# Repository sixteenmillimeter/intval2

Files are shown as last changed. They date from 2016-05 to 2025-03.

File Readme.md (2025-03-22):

# INTVAL 2.0
##### Intervalometer for Bolex 16mm Cameras

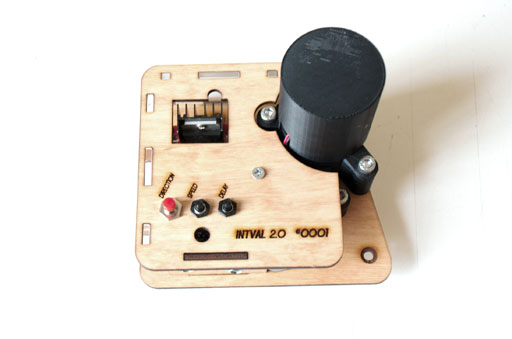
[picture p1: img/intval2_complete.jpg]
Photo of finished INTVAL


## [Project Home - git.sixteenmillimeter.com/16mm/intval2](https://git.sixteenmillimeter.com/16mm/intval2)

#### Github Mirror - [github.com/sixteenmillimeter/intval2](https://github.com/sixteenmillimeter/intval2)

----

 1. [Overview](#Overview)
 2. [Attachment](#Attachment)
 3. [Usage](#Usage)
 4. [Power](#Power)
 5. [Creating Your Own](#Creating)

----
### 1) Overview 

The INTVAL 2.0 is an open-source open-hardware intervalometer for Bolex 
16mm cameras. It enables you to expose single frames of film
at a regulated interval. Utilizing the 1:1 shaft in Bolex cameras (**Rex
4 and later models**) the INTVAL 2.0 can complete a full rotation of the shutter
in either 1 or 2 seconds. This allows for a range of long exposure options when
used in concert with the Rexofader.

----
### 2) Attachment

To attach the INTVAL 2.0 to a Bolex camera, disable the motor and line up the four standoffs
with the mounting holes on the body of the camera and insert the key into the 1:1 shaft. 
This can be done by laying the camera on its side--with the mounting holes facing up--and placing the INTVAL 2.0 on top of the body and making sure the key fits into the slotted 1:1 opening.
If you have never attached anything to the mounts before, you may have to 
remove small screws that are in the holes. This opens up the mounting holes for 
the screws that will hold the intervalometer in place. There are four standoffs
and screws, but only three need to be attached to maintain the hold required for operation.

----
### 3) Usage

The INTVAL 2.0 has two physical interfaces: the buttons on the case and the shutter
release cable. The shutter release cable plugs into the underside of the case, next
to the DC adapter, and triggers the camera. A single, short press will trigger a ``single
frame``. Holding down the shutter release for more than 1 second will start a ``continuous sequence``
of frames. Hitting the shutter release during a running sequence will stop the intervalometer.

The buttons on the case control three variables: direction, speed and delay. The direction of the
camera can be set to ``forwards`` (default) with a quick press, and set to ``backwards`` by holding the
button for more than 1 second. 

Similarly, the speed can be set to ``1 second rotation`` (default) with a
quick press and set to ``2 second rotation`` by holding the button for more than 1 second. Remember,
during the 1 or 2 seconds that the shutter is rotating, exposure only occurs for a fraction of that time. How large a fraction depends on the setting of the Rexofader.

Delay refers to the time the intervalometer pauses between frames and only matters when running a sequence. The delay is set to ``42 ms`` by default and will be set to however long you hold it down for; holding the button for``10 seconds`` will set the delay between each frame to ``10 seconds``. Pressing the button quickly will reset the timer to the default ``42 ms``.

----
### 4) Power

Power the INTVAL 2.0 with 12VDC to the 2.1mm DC power jack located on the bottom of the case.
The maximum draw of the motor is under 1 Amp, so that much current should be ample to run the
intervalometer. Portable batteries, such as those used as supplimental cellphone power supplies, 
can be used to as mobile power sources, but they must be able to provide 12V and not the typical 5V that many of these batteries provide. 

Two examples: 

[Anker 2nd Gen Astro Pro2 20000mAh 4-Port Aluminum Portable External Battery Charger with 9V/12V Multi-Voltage Port](http://www.amazon.com/gp/product/B005NGLTZQ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)

[ Rechargeable 3800mAh Lithium Ion Battery Pack with DC Connector, 12 volt](http://www.amazon.com/gp/product/B007RQW5WG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)

12V wall warts that can provide 1 Amp or over are also viable options for shooting in a controlled environment.

----
### 5) Creating Your Own

All parts of the INTVAL 2.0 are reproducible via 3D printing, laser cutting or are purchasable (example links are to Amazon or [Adafruit](http://adafruit.com)) for a total build cost of ~$50. The files in this repository consist of .SCAD, .STL, .DXF and .INO files. The .SCAD files contain all the elements needed to generate the physical body of the intervalometer with .DXF files for
laser cutting and .STL files for 3D printing. The .INO file contains the source code for the Arduino sketch that powers the INTVAL 2.0.

#### A. 3D Printing

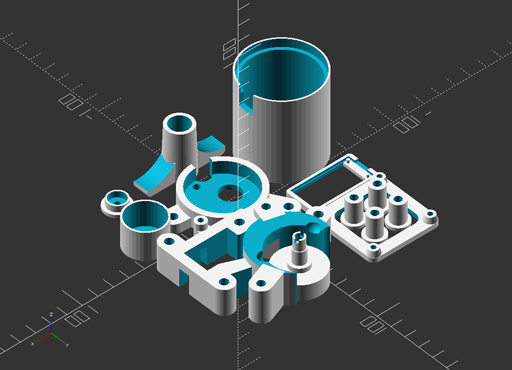
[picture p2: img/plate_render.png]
Plate of all 3D printed components


The most time-consuming part of this build *should* be 3D printing the parts for the INTVAL 2.0. Depending on the size of your printing bed it is most likely possible to print all parts in one convenient plate. As will be addressed later, the laser-cuttable elements can also be 3D printed if you lack access to a laser cutter. 

In the ``/dist`` directory of the repo, you will find all of the .STL files needed to build the intervalometer. If needed, the .SCAD file can be used to generate additional .STL models, or it can be modified to produce unique parts to your own specifications.

The most delicate and integral piece to be fabricated on a 3D printer is the ``motor_key``, which interfaces the intervalometer to the 1:1 shaft of the Bolex. This part should be printed as close to solid as your printer allows or you should look at a third-party printing service to have it made from stronger materials than the typical PLA or ABS used by most home printers. That said, I have used an ABS-printed motor key extensively with no issues thus far.

#### B. Laser Cutting

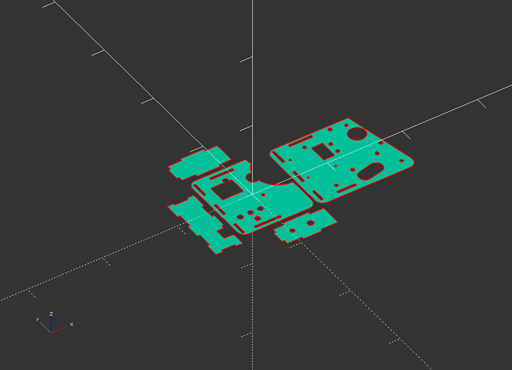
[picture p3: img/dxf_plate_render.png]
Plate of all laser cut components


The INTVAL 2.0 has a flat panel on which all parts and electronics are mounted. For this reason, and to reduce production time, a laser cutting component has been added. See the much earlier--and now deprecated--attempt to have an entirely printable model in the original [INTVAL](https://github.com/sixteenmillimeter/INTVAL) (or [INTVAL Next](http://www.thingiverse.com/thing:151944) as I had taken to calling it on [Thingiverse](http://thingiverse.com)). Printing the flat base of this version took upwards of 3 hours on my modest printer, and with the accessibility of laser cutters at hacker/maker spaces becoming more common I decided this was feasible to include in my design.

Important to note: **A laser cutter is not required to make this intervalometer.** If you have access to a 3D printer, it's very possible to use the .SCAD files to generate .STLs of the parts designated for cutting. Make sure that they are all set to 3.175mm thickness as the design requires 1/8" materials for assembly. A clever person could even improve the design to remove the need for bolts to attach the ``motor_mount_bottom`` and ``electronics_mount`` pieces when making a 3D printed version.

Another note: When cutting the base of the intervalometer, named the ``panel_laser`` there is a circular cut for a skateboard wheel bearing to be inserted. These are made with slightly different tolerances, so do some tests before you cut your final panel. When properly scaled, the bearing should fit tightly so that it can be glued to the panel. The positioning of the bearing is vital to the functionality, so it's best to test the bearing fit using the ``bearing_calibrate`` module and then edit the size of the bearing by changing the  ``fuzz`` variable of the ``bearing_laser`` module. Export a new .DXF of the ``intval_panel_laser`` module by using the ``projection()`` function and cut that.

##### Materials

Early prototypes for the INTVAL 2.0 were made with 1/8" acrylic. I was very hopeful that I would be able to make a visually clear product where all of the electronics would be visible. Cool, right? This, unfortunately, was not to be. The forces applied to the prototypes during casual use would cause the acrylic to crack or shatter quite easily. I'm not saying it's not possible, but just that it is a less-than-ideal material for this project.

Here's what I would suggest, in order (all should be cut from 1/8" sheets):

 1. Craft plywood - Cheap, flexible and effective. I cut this, add custom designs, stain and coat in polyurethane. Yet to have any issues with it.
 2. Delrin (acetal homopolymer) - Too rich for my blood, but should perform better than acrylic. Will probably look pretty cool.
 3. Acrylic - Good for prototyping, but may crack under pressure. Make parts to spare if you go down this path.

#### C. Hardware

I would like to further reduce the amount of non-fabricated parts required for this build in future revisions, but here we are. I've run a few spreadsheet models and have the cost-per-unit down to ~$50, but this fails to account for shipping, misprints and a whole host of associated costs, including build time. Needless to say, I don't see a profitable enterprise being build on the production of 16mm intervalometers, which is why I am creating this in the open for others to build and improve upon. 

Links below are to Amazon for accessibility and [Adafruit](http://adafruit.com) where possible, but feel free source compatible or equivalent materials from companies that align to your personal ethics. Sourcing from AliExpress can bring the cost-per-unit down dramatically, if you are building these as part of a workshop or class.

The meat of this project are the L298N Dual H-Bridge and the Arduino Trinket 5V. The 3D models are designed for the 60RPM motor listed below, but the design can easily be adapted to other motors. I'm trying out other motors in a few different forks of this project.

All of the purchasable parts for this build:

1. (1x) Arduino Trinket Pro 5V - [[Adafruit](https://www.adafruit.com/products/2000)] [[Amazon](https://amzn.to/2WdVimL)]
3. (1x) 120RPM 12VDC Motor - [[Amazon](https://amzn.to/2YDGFe2)]
4. (1x) L298N Breakout Board - [[BC Robotics](https://www.bc-robotics.com/shop/l298n-motor-driver-board/)] [[Amazon](https://amzn.to/35CRFKa)]
5. (1x) Microswitch w/ Roller - [[Adafruit](https://www.adafruit.com/product/819)] [[Amazon](https://amzn.to/2YDGFe2)]
6. (1x) 3.5mm Socket Audio Connector - [[Amazon](https://amzn.to/2SGFVAY)]
7. (1x) 3.5mm Stereo Audio Cable - [[Amazon](https://amzn.to/3beNPrQ)]
8. (4x) Momentary Push Button 7mm Diameter - [[Amazon](https://amzn.to/2LavqBK)]
 8. (1x) Micro Switch w/ Roller Lever 28mm x 30.2mm x 10.2mm - [[Adafruit](https://www.adafruit.com/products/819)] [[Amazon](https://amzn.to/2SMBFzX)]
 9. (1x) Skateboard bearing 608-2RS - [[Amazon](https://amzn.to/3b7X2lC)]
 10. (4x) M3.5 - 0.6 x 20mm Screws
 11. (3x) M2 - 0.6 x 15mm Bolts
 12. (6x) M5 - 0.8 x 25mm Bolts
 13. (4x) M5 - 0.8 Nuts

Additionally you'll need wire and solder of your choosing.

#### D. Assembly

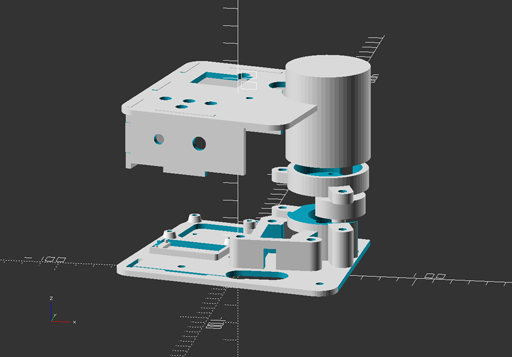
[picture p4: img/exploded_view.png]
Photo of exploded view


Assembling the INTVAL 2.0 can be done in an hour or so, much quicker if practiced. As mentioned, the largest amount of time should be in fabricating the parts or acquiring electronics/parts. There are 2 things I don't like about this design that I'll be addressing in subsequent builds: complexity of the electronics and crowding inside the case.

##### **Mounting the electronics**

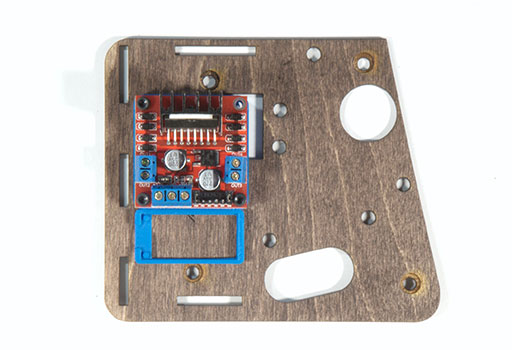
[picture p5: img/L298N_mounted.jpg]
Photo of L298N mounted to panel


The L298N is attached to the panel via the three M2 bolts. The space cut in the panel where the fourth would go is to prevent the Bolex's handle from rubbing against the panel. At this point I usually flash the Arduino Trinket Pro with the latest firmware, as in the ["Programming"](#Programming) section, prior to soldering and mounting. It can be done after, though, and can be reprogrammed after it is built.

##### **Attaching the bearing**

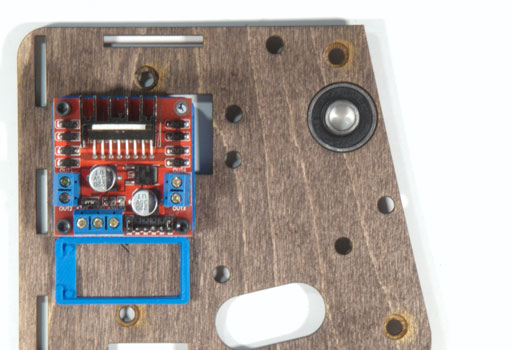
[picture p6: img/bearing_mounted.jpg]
Photo of panel with bearing attached


##### **Mounting the motor's base and microswitch**

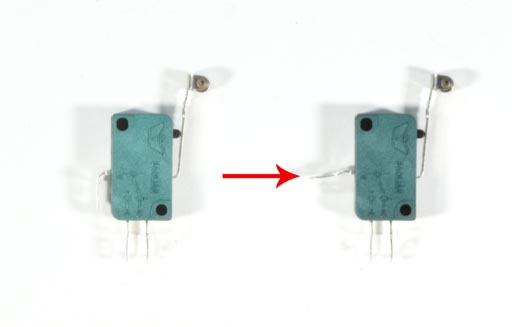
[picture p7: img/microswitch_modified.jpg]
Photo of Microswitch and modification made to it


Modify the microswitch as shown in the photos. Be careful not to break the tab by over-exerting it at the bend. At this point, I usually solder leads onto the two tabs as shown below to save a cramped soldering job later. Insert the microswitch into the ``motor_mount_bottom`` and line the piece up with the 6 holes cut in the panel according to the pictures and rendering. It then gets attached to the panel with 4 of the M5 bolts and attached on the bottom with the corresponding M5 nuts.

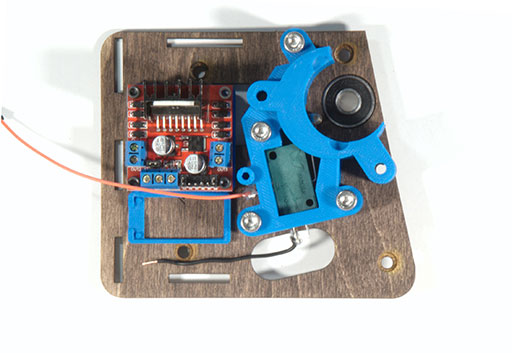
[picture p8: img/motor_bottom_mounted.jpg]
Photo of panel with motor mount bottom attached


##### **Mounting the motor**

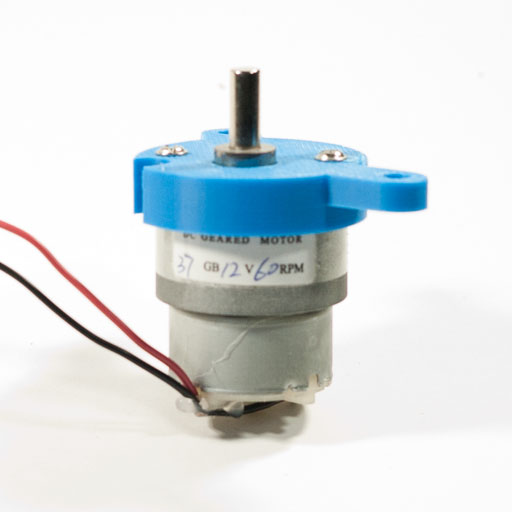
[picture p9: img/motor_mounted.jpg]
Photo of motor ready to mount on panel


The motor should fit snugly into the ``motor_mount`` piece and can be attached with 2 screws that usually accompany the motor (when bought from Amazon). At this point, I usually solder 2 leads onto the top of the motor and cap it so that the fragile tabs wont break off. I use red and black wires so that I can easily switch their position in the L298N if the intervalometer is functioning backwards.

##### **Attach buttons**

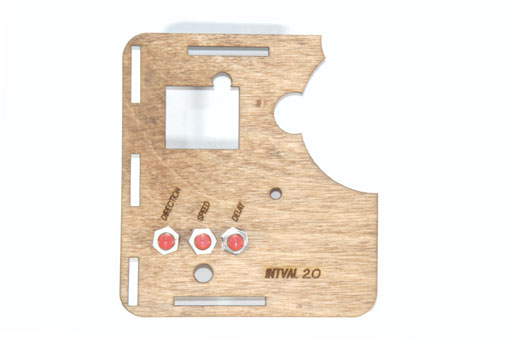
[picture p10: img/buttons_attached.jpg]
Photo of buttons attached to panel cover


Three of the buttons are attached to the corresponding holes in the panel. The size of these holes might have to be modified depending on the type of momentary buttons you settle on. When cutting the panel cover, I will also add an etched-in label for each specifying (left to right) that they control ``direction``, ``speed``, and ``delay``.

##### **Attaching the DC and 3.5mm sockets**

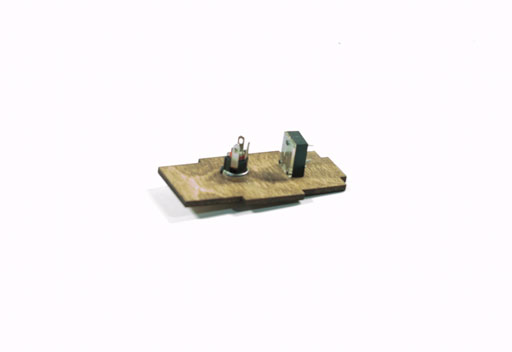
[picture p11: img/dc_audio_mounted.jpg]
Photo of DC and 3.5mm sockets on


Attach the 2.1mm DC socket and the 3.5mm audio socket to the bottom panel of the board, using the bolts to secure them. 

#### E. Soldering

Use of the $10 [Arduino Trinket Pro 5V](https://www.adafruit.com/products/2000) is explicitly due to the number of buttons required for the user interface. If you wanted to drop one of the buttons, say the speed control, you could re-write the sketch to use a $7 [Arduino Trinket 5V](https://www.adafruit.com/products/1501) (or get them in bulk for more savings). I mention this because it was the target microcontroller breakout for the project but had to be upgraded to the pro model to support all of the features in the design.

Digital pin utilization is as follows:

- **PIN 3** - Shutter release
- **PIN 4** - Delay button
- **PIN 5** - Speed button
- **PIN 6** - Direction button
- **PIN 9** - Motor forward (L298N)
- **PIN 10** - Motor backward (L298N)
- **PIN 13** - LED indicator (built in to Trinket Pro)
- **PIN 19** - Microswitch (aka A5)

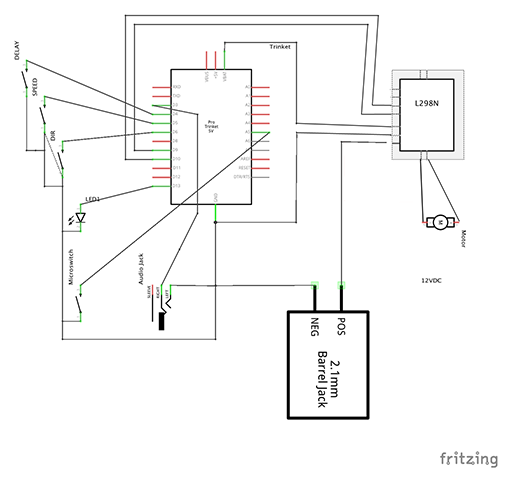
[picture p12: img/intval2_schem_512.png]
Fritzing schematic


The Fritzing project requires the following libraries:

 1. [Adafruit Fritzing library](https://github.com/adafruit/Fritzing-Library)
 2. [L298N Dual H-Bridge library](https://github.com/yohendry/arduino_L298N)

#### E. Building the shutter release (plunger)

To trigger the intervalometer and to start/stop sequences, the INTVAL 2.0 uses a simple switch that I found is handily made from cheap audio parts. In a pinch, this switch can be hard-wired into the design, but for the safety of the electronics inside I decided on using a 3.5mm socket and 3.5mm cable with a simple momentary button closing the circuit. For this, I buy a 6' cable and cut it in two.

Pull the cable through the small bottom cap of the plunger body (important) and solder both of the leads to the two tabs of the button. The bottom cap might have to be modified to better accommodate the size of the 3.5mm audio cable you end up using. Insert the button into the plunger body and fasten with the nut provided with the button. Then attach the bottom cap to the body. At this point, I usually use hot glue to prevent too much force being applied to the solder points.

#### G. Programming

This step should be done carefully, and with some practice. For a good primer on the basics of programming the microcontroller, check out Adafruit's [tutorial on it](https://learn.adafruit.com/introducing-pro-trinket/starting-the-bootloader). Arduino Trinket Pros enter into a short firmware-writable state when first plugged into a USB source. This is marked by the pulsing of the red indicator LED on the board.

If using the Arduino IDE, make sure you have the latest version and have read through [this primer](https://learn.adafruit.com/introducing-pro-trinket/setting-up-arduino-ide) before you try to upload the sketch to the Trinket Pro. While the red LED is flashing, upload the sketch provided in this repository and that's it. Any modifications to the code can be made and flashed onto the board as many times as you'd like. Please feel free to submit pull requests if you make any improvements!

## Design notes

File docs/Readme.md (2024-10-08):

# intval2 Quickstart

## Attaching

1. Disengage the Bolex motor by switching the lever at position **M** to **O**.
2. Set the camera trigger to **M** (opposite **P**).
3. Place the intval2 on the camera, lining up the 4 standoff posts with the 4 exposed metal mounting points.
4. Line up the intval2 key to the Bolex 1:1 shaft so that it fits snugly.
5. Place the 3.5mm screws into 3 of the standoffs, one above the 1:1 shaft, one below and the other in the back top area of the intval2. The standoff underneath the buttons is not accessible.
6. Tighten the 3.5mm screws to secure the intval2 to the Bolex.

## Powering

Power the device using a 12V DC power source with a 2.1mm center-positive barrel connector.
Ensure that the power supply can output at least 1 Amp to ensure there is enough force to drive the motor.
You can use a portable battery designed for recharging phones as long as it is capable of outputting 12V.

Plugging and unplugging the shutter release cable will trigger a frame so ensure that it is plugged in before powering on and removed before powering off if you do not want to unexpectedly advance or rewind the camera.

## Using

Using the intval2 is simple and relies on the settings made available by the 3 buttons on the side and the shutter release cable.

### Shutter Release

The shutter release cable uses a 3.5mm audio cable and a simple switch to trigger a frame.
Pressing the shutter release cable button for longer than 1 second and releasing starts timelapse mode where the camera will shoot frames continuously.
The other buttons change settings that will take effect when you trigger each frame.

Keep in mind that plugging and unplugging the cable while the intval2 is powered on and attached to a Bolex will trigger a frame.

### Direction

The direction button, labeled "DIR" and usually red, will change the direction of the camera from forward to reverse by pressing it for longer than 1 second.
Press it for less than 1 second to reset it to forward.

### Exposure

In normal mode the camera completes a frame in ~500ms, which after accounting for the shutter angle and the prism light loss, is roughly equivalent to 1/5 second exposure.

Change the exposure of the camera by pressing the button "EXP", usually green, for longer than 1 second.
However long you press the button is how long an exposure the camera will make.
Once set an exposure will be taken by opening the shutter, waiting for the appropriate amount of time, and then closing the shutter.
Press the button for less than 1 second to restore normal exposure.

### Delay

The "delay" feature determines how long between frames the intval2 will wait when running in timelapse mode.

Change the delay between frames by pressing the "DEL" button, usually blue, for longer than 1 second.
Similar to the others, press it for less than 1 second to reset the delay to 0.

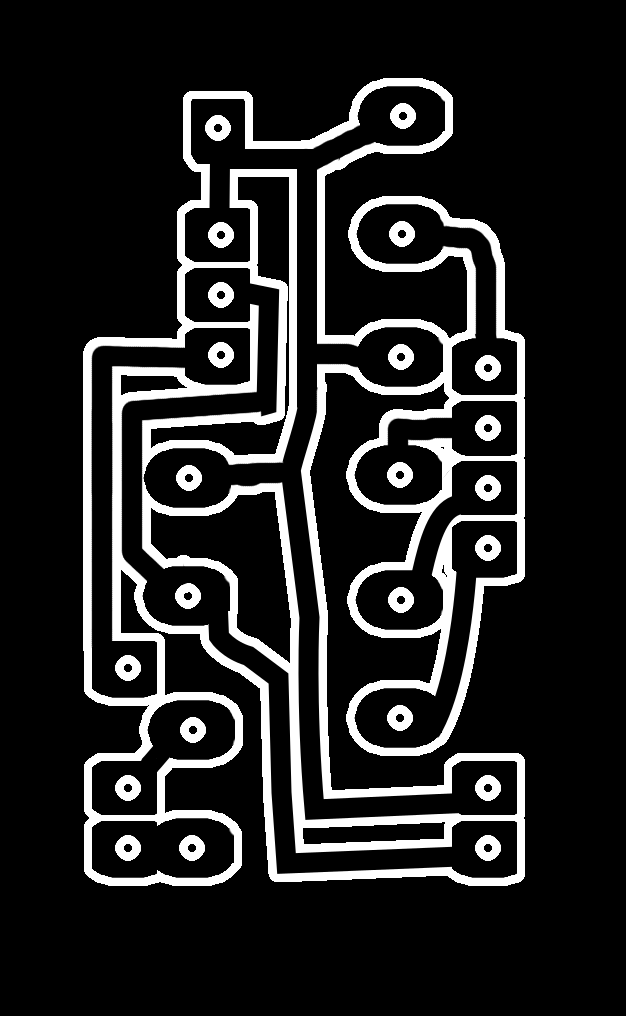
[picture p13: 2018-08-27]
dist/intval2_shield_etching/intval2_shield_servo_v2.png

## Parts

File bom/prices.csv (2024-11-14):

part | part_id | price | url
DC Power Jack | N/A | 110 | https://amzn.to/4evqnHx
12V 120RPM Geared Motor 37mm Gearbox | N/A | 1499 | https://amzn.to/3YQo1ge

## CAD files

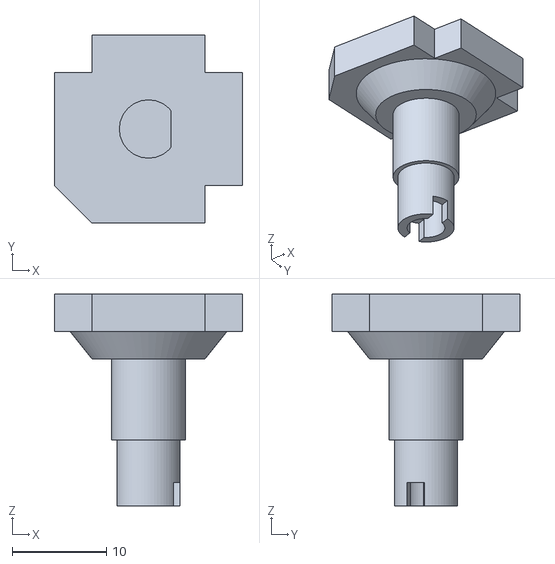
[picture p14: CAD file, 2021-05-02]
dist/intval2_motor_key_reinforced.stl
20.0 x 20.0 x 22.5

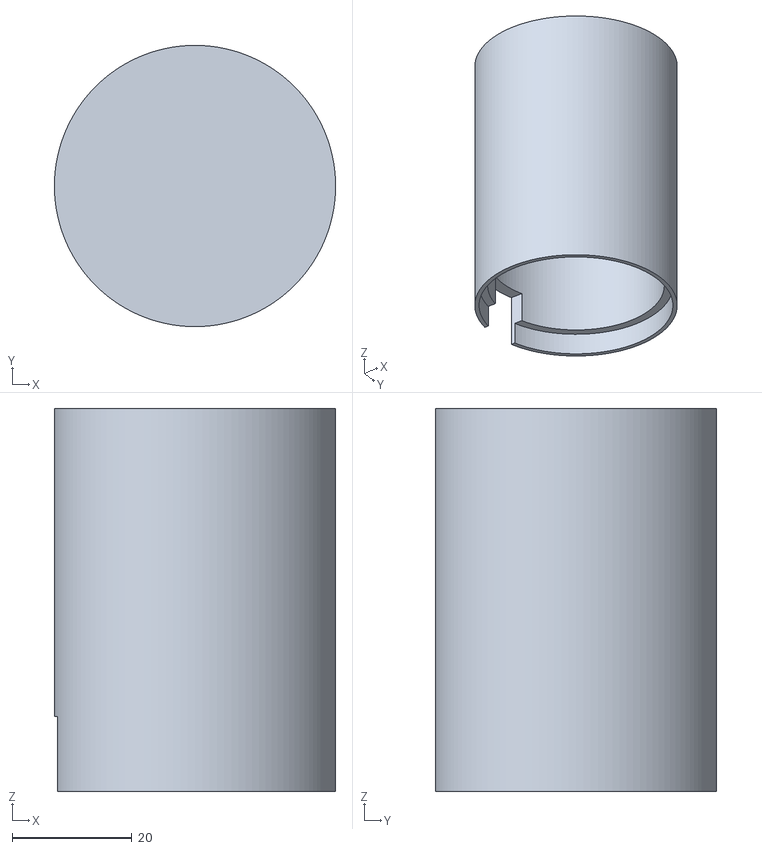
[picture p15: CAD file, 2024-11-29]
stl/intval2_motor_cap_alt.stl
47.0 x 47.0 x 64.0

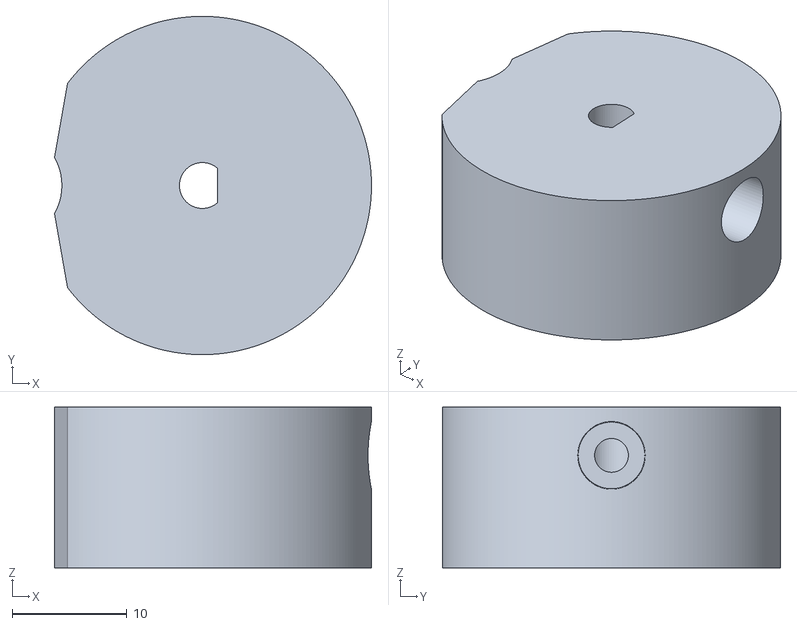
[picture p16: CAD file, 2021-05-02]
dist/intval2_motor_key_120_reinforced_roller.stl
27.6 x 29.5 x 14.0

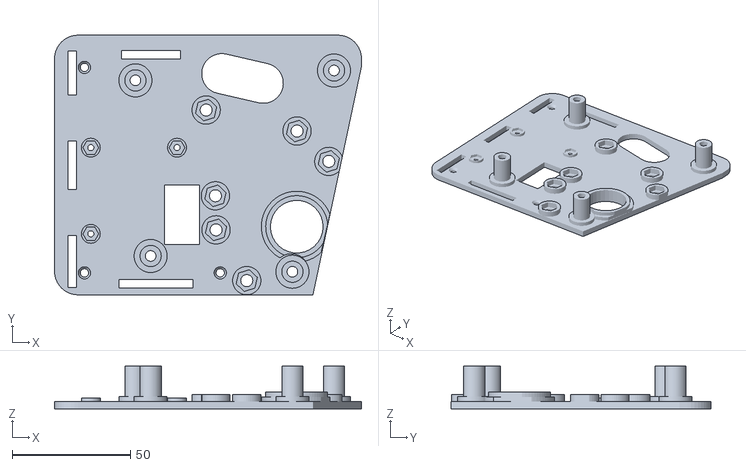
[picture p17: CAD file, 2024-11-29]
stl/intval2_printed_panel.stl
130.0 x 110.0 x 18.2

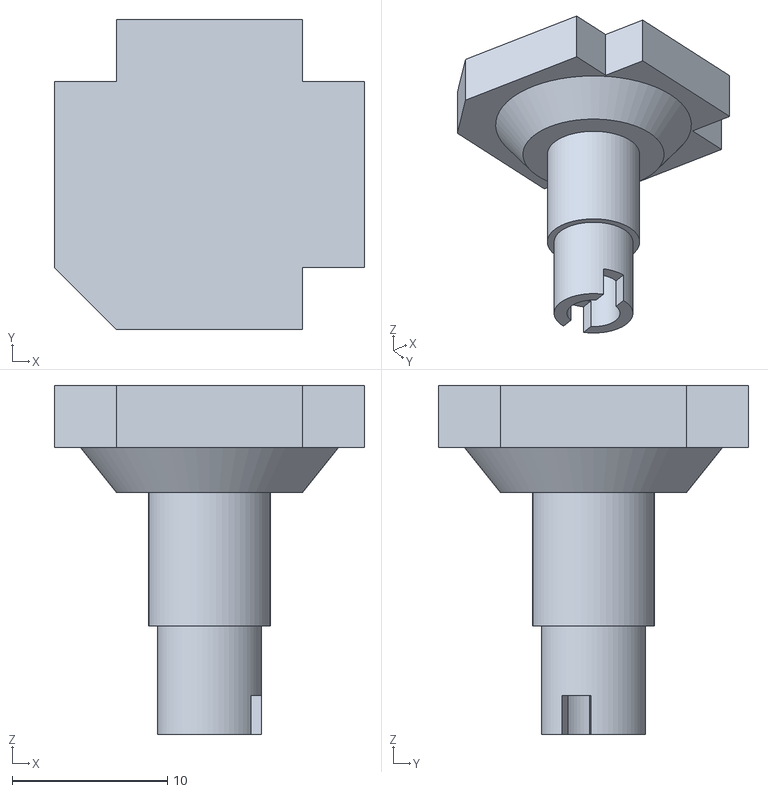
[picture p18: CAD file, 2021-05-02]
dist/intval2_motor_key_120_reinforced.stl
20.0 x 20.0 x 22.5

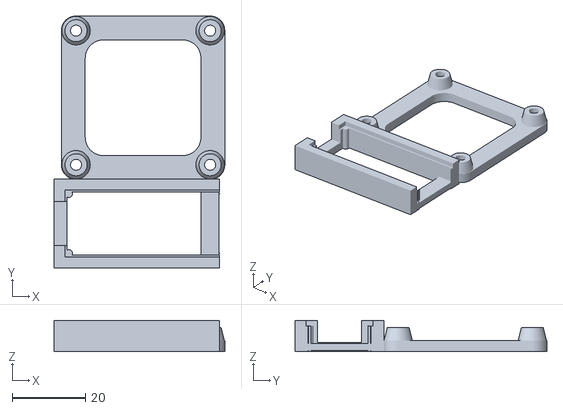
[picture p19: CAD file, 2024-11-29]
stl/intval2_arduino_nano_electronics_mount.stl
46.5 x 68.6 x 8.50

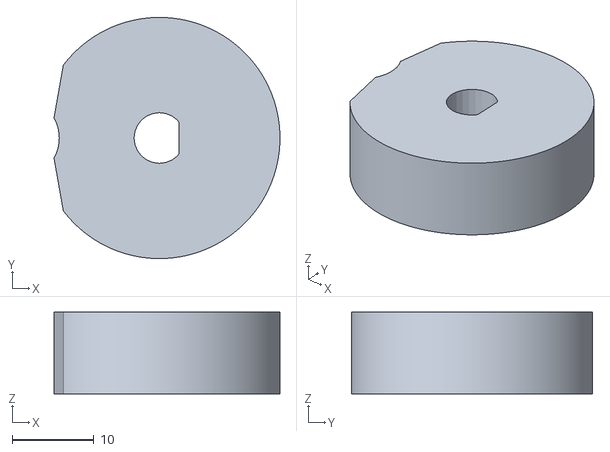
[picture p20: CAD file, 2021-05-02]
dist/intval2_motor_key_reinforced_roller.stl
27.6 x 29.5 x 10.0

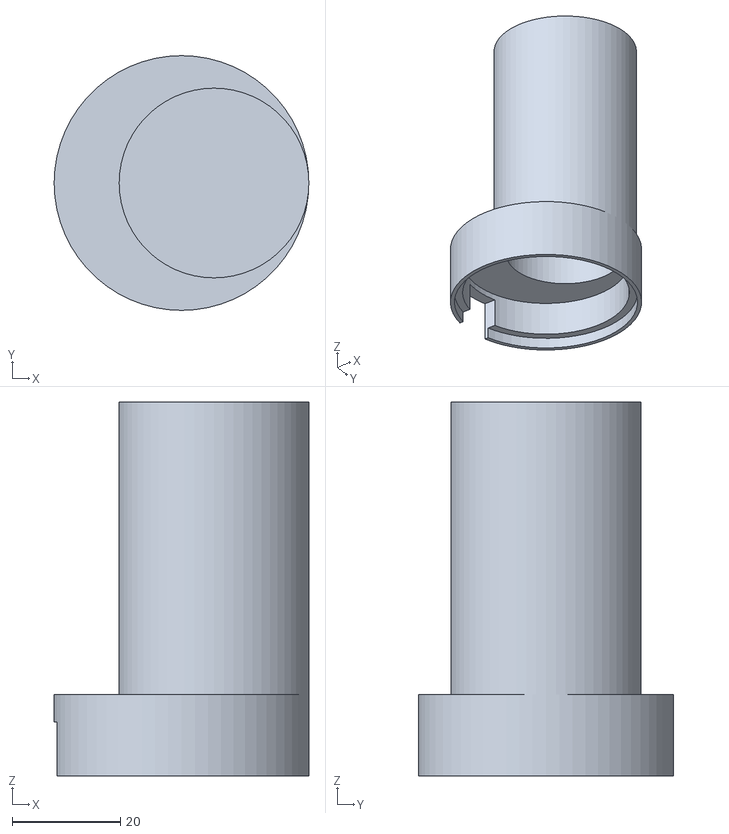
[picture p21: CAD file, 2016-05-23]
dist/intval2_motor_cap_120.stl
47.0 x 47.0 x 69.0

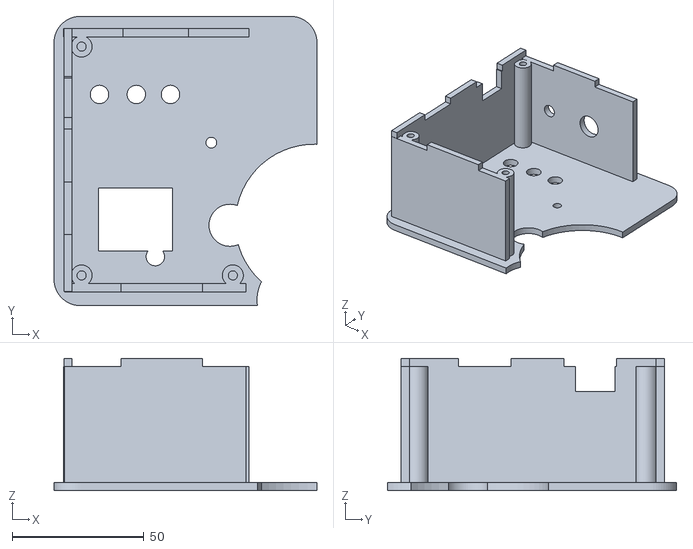
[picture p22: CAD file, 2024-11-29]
stl/intval2_printed_panel_cover_buttons.stl
100.0 x 110.0 x 50.4

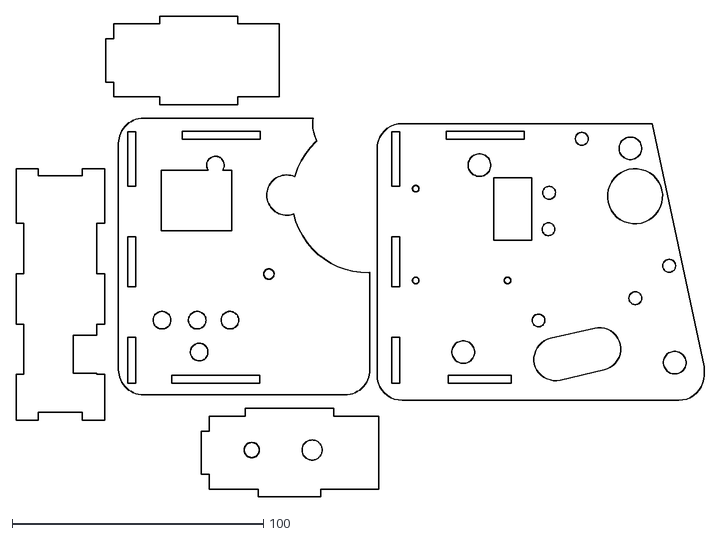
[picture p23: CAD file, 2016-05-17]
dist/intval2_dxf_plate.dxf
273.6 x 191.2

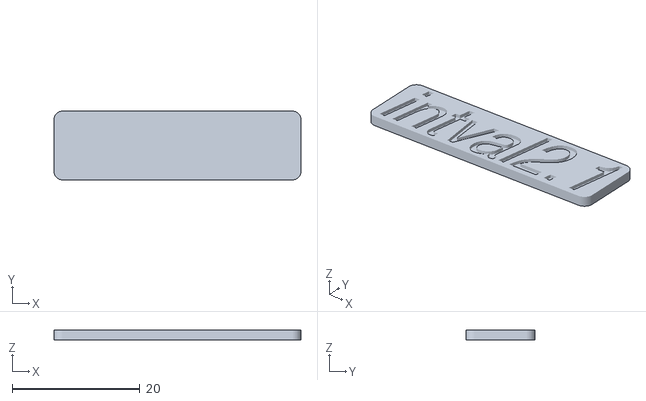
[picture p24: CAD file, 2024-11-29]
stl/intval2_logo.stl
38.7 x 10.8 x 1.50

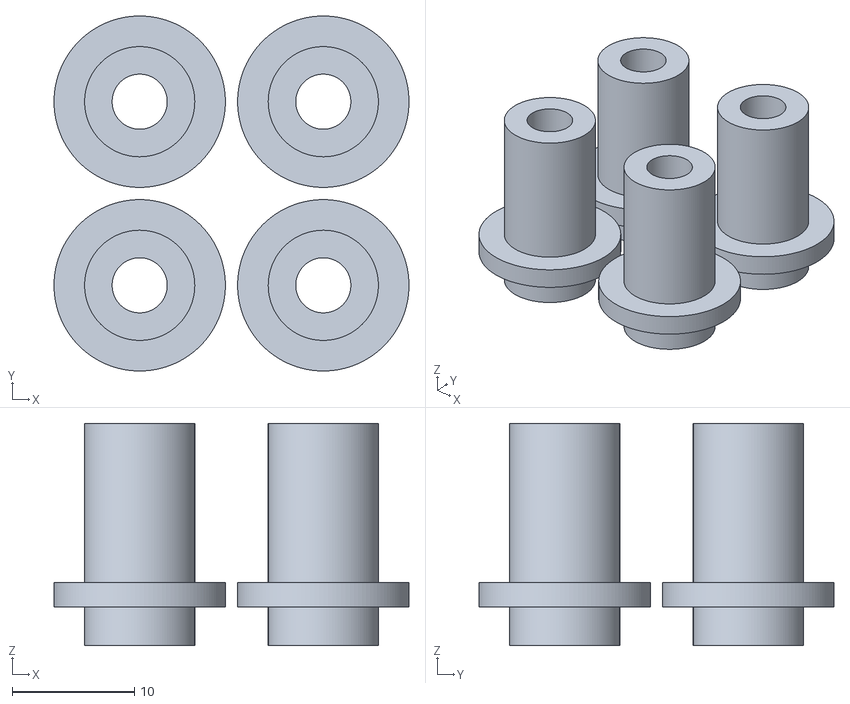
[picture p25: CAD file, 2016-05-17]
dist/intval2_standoffs.stl
29.0 x 29.0 x 18.2

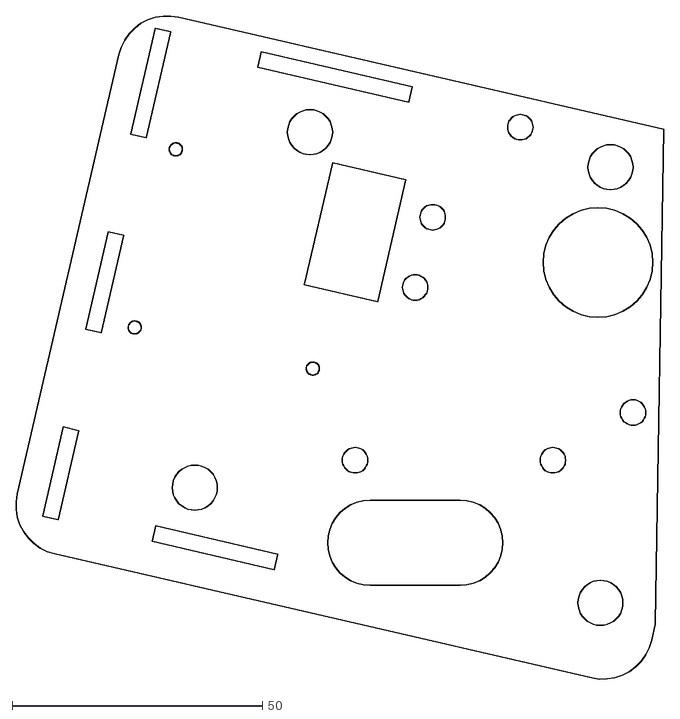
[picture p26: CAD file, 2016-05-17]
dist/intval2_panel_laser.dxf
129.4 x 132.4

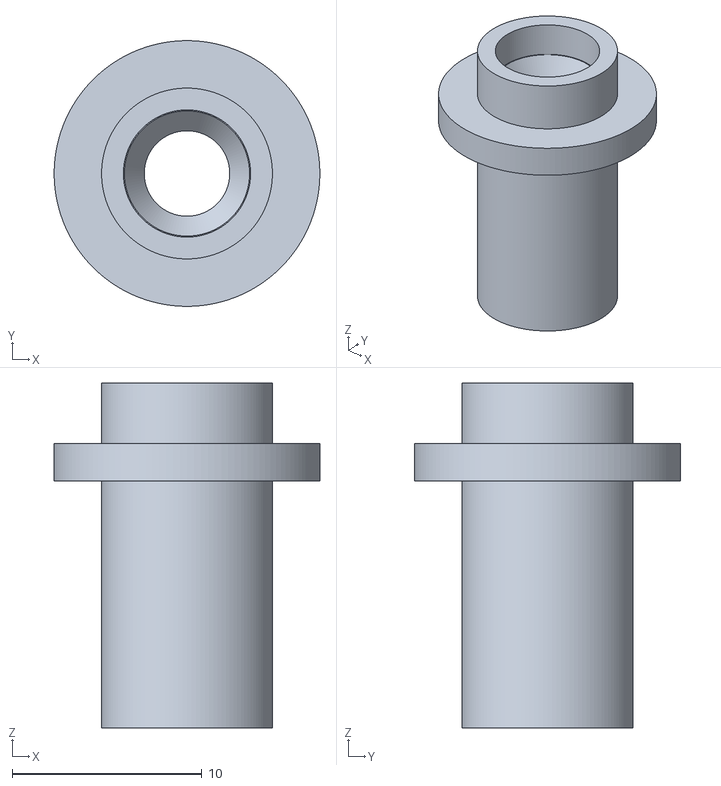
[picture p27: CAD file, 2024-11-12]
stl/intval2_standoff.stl
14.0 x 14.0 x 18.2

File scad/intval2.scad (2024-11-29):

include <./ready.scad>

mm_x = [61.5, 21.5, 6, 45.5, 18, 39];
mm_y = [-18, 21, -27.5, -27.5, 7, 39];
mm_r = [110, -15, 0, 0, 0, -70];
mm_l = [13, 9, 0, 0, 0, 8];
//xArray = [-3, 57,  55,  10, -26]; //WITH MIDDLE PIN
//yArray = [38, 31, -56, -22, -33]; //WITH MIDDLE PIN
xArray = [-3, 57,  55,  -26]; //NO MIDDLE PIN
yArray = [38, 31, -56,  -33]; //NO MIDDLE PIN

outerD = 9;
innerD = 4.5;
height = 17;

//panel_x = 129 + 4;
//panel_y = 131;
panel_2_x = 110;
panel_2_y = 110;

one_to_one_x = 54.5;
one_to_one_y = 12;

bolt_inner = 2.55;

screw_distance = 31;

module m5_nut_void (pos = [0, 0, 0]) {
    translate(pos) cylinder(r = 9.4 / 2, h = 4, $fn = 6, center = true);
}

module m5_nut_seat (pos = [0, 0, 0]) {
    $fn = 40;
    H = 4;
    translate(pos) difference () {
        cylinder(r = 12 / 2, h = H, center = true);
        cylinder(r = bolt_inner, h = H + 1, center = true);
        rotate([0, 0, 30]) m5_nut_void([0, 0, -1]);
    }
}

module m3_nut_void (pos = [0, 0, 0]) {
    translate(pos) cylinder(r = 6.7 / 2, h=3, center=true, $fn=6);
}

module m3_nut_seat (pos = [0, 0, 0]) {
    $fn = 40;
    H = 3;
    translate(pos) difference () {
        cylinder(r = 8 / 2, h = H, center = true);
        cylinder(r = 3.25 / 2, h = H + 1, center = true);
        m3_nut_void([0, 0, -1]);
    }
}

module l298N_nut_seats (r = 3/2 - .2, MOD_MOUNT = 0) {
    DISTANCE = 36.5 + MOD_MOUNT;

    m3_nut_seat([0, 0, 0]);
    m3_nut_seat([DISTANCE, 0, 0]);
    //m3_nut_seat([DISTANCE, DISTANCE, 0]);
    m3_nut_seat([0, DISTANCE, 0]);
}

module arduino_nano_mount (pos = [0, 0, 0]) {
    X = 18.2;
    Y = 43.9;
    Z = 10.5;
    BOARD_Z = 1.5;
    translate(pos) {
        difference () {
            //outer
            cube([X + 6, Y + 6, Z], center = true);
            //inner void minus corners
            difference () {
                cube([X - 1, Y - 1, Z + 1], center = true);
                translate([(X / 2) - 1, (Y / 2) - 1, -BOARD_Z]) cylinder(r = R(2), h = Z + 1, center = true, $fn = 20);
                translate([(-X / 2) + 1, (Y / 2) - 1, -BOARD_Z]) cylinder(r = R(2), h = Z + 1, center = true, $fn = 20);
                translate([(X / 2) - 1, (-Y / 2) + 1, -BOARD_Z]) cylinder(r = R(2), h = Z + 1, center = true, $fn = 20);
                translate([(-X / 2) + 1, (-Y / 2) + 1, -BOARD_Z]) cylinder(r = R(2), h = Z + 1, center = true, $fn = 20);
            }
            //board void
            translate([0, 0, (Z / 2) - (BOARD_Z / 2)]) cube([X, Y, BOARD_Z], center = true);
            //usb void
            translate([0, Y / 2, (Z / 2) - (6 / 2) + 0.01]) cube([12, 10, 6], center = true);
            translate([0, -30, 0]) cube([30, 20, 20], center = true);
        }
        translate([0, -(Y/2) + 4.5, -2]) cube([X + 5, 5, 2], center = true);
    }
}

module usb_mini_void (pos = [0, 0, 0]) {
    translate(pos) {
        translate([0, 25, 2]) {
            cube([8, 10, 5], center = true);
            translate([0, 5, 0]) cube([12, 10, 8], center = true);
        }
    }
}

module intval_panel_printed () {
	difference () {
        union () {
            intval_panel_laser(0.4);
		    for (i = [0 : len(mm_x) - 1]) {
                m5_nut_seat([mm_x[i], mm_y[i], 6]);
            }
            translate([-38, -1, 7]) rotate([0, 0, -13]) l298N_nut_seats();
            translate([0, 0, -0.6]) intval_laser_standoffs();
            translate([one_to_one_x, one_to_one_y, 5]) rotate([180, 0, 0]) bearing_reinforcement();
        }
        //onetoone(9, 14, 8.5);
		bearing(54.5, 12, 6, width= 18, hole=false);
		//frame_counter_access(); //use the space
		remove_front();
        printed_panel_bolts();
	}
}

module l298N_bolt_voids (r = 3/2 - .2, MOD_MOUNT = 0) {
    $fn = 60;
    DISTANCE = 36.5 + MOD_MOUNT;
    H = 50;
    translate([0, 0, 0]) cylinder(r = r, h = H * 5, center = true);
    translate([DISTANCE, 0, 0]) cylinder(r = r, h = H * 5, center = true);
    translate([DISTANCE, DISTANCE, 0]) cylinder(r = r, h = H * 5, center = true);
    translate([0, DISTANCE, 0]) cylinder(r = r, h = H * 5, center = true);
}

module l298N_hole_test () {
    $fn = 40;
    difference () {
        cube([140, 40, 3], center = true);
        cylinder(r = R(3), h = 50, center = true);
        for (i = [0 : 3]) {
            translate([7 + (i * 7), 0, 0]) cylinder(r = R(3) - (0.1 * i), h = 50, center = true);
        }
    }
}

module intval_panel_laser (pad = 0) {
    $fn = 40;
	difference () {
		union () {
			difference () {
				translate ([0, 0, 8.5]) {
					union () {
						translate([12, -5, 0]) {
                            rotate([0, 0, -13]) {
                                rounded_cube([panel_2_x + 20, panel_2_y, 25.4 / 8], d = 20, center = true);
                            }
                        }
					}
				}
				for (i = [0 : len(xArray) - 1]) {
					bolex_pin_inner_laser(xArray[i], yArray[i]);
				}
			}
		}
		bearing_laser(54.5, 12, 6, width= 18, hole=false);
        translate([-38, -1, 0]) rotate([0, 0, -13]) l298N_bolt_voids();
		m_p_access();
		remove_front();
		translate([6, 18, 0]) rotate([0, 0, -13]) cube([15, 25, 40], center=true); //motor wind key hole

		for (i = [0 : len(mm_x) - 1]) {
			translate([mm_x[i], mm_y[i], 0]) cylinder(r = bolt_inner, h = 100, center = true);
		}
        translate([0, 0, 0.3]) scale([1, 1, 1]) intval_laser_panel_cover(PAD = pad, BOLTS = false);
	}
}

module intval_panel_laser_debug () {
    $fn = 40;
	difference () {
		union () {
			difference () {
				translate ([0, 0, 8.5]) {
					union () {
						translate([-20.5, 4, 0]) {
                            rotate([0, 0, -13]) {
                                rounded_cube([panel_2_x + 85, panel_2_y, 25.4 / 8], d = 20, center = true);
                            }
                        }
						//reinforces
						//translate([54, -12, -3]) rotate([0, 0, 89]) rounded_cube([110, 20, 4], 20, center = true);
						//translate([-17, 2, -3]) rotate([0, 0, 72]) rounded_cube([94, 13, 4], 13, center = true);
					}
				}
				for (i = [0 : len(xArray) - 1]) {
					bolex_pin_inner_laser(xArray[i], yArray[i]);
				}
			}
			//onetoone(26, 10, 4.5);
			//extends for onetoone
			

		}
		//onetoone(9, 14, 8.5);
		bearing_laser(54.5, 12, 6, width= 18, hole=false);
        translate([-38, -1, 0]) rotate([0, 0, -13]) l298N_bolt_voids();
        //translate ([6, -9, height + 3.5]) cylinder(r = bolt_inner, h = 50, center = true); //cover standoff hole
		//frame_counter_access(); //use the space
		m_p_access();
		remove_front();
		translate([6, 18, 0]) rotate([0, 0, -13]) cube([15, 25, 40], center = true); //motor wind key hole

		for (i = [0 : len(mm_x) - 1]) {
			translate([mm_x[i], mm_y[i], 0]) cylinder(r = bolt_inner, h = 100, center = true);
		}
        intval_laser_panel_cover(DEBUG = true);
        translate ([4, 12, 0]) {
            translate([-51.5, -8.5, 0]) cylinder(r = R(2.8), h = 100, center = true);
            translate([-117.5, 6.5, 0]) cylinder(r = R(2.8), h = 100, center = true);
            translate([-40.0, 41, 0]) cylinder(r = R(2.8), h = 100, center = true);
            translate([-106.0, 56.5, 0]) cylinder(r = R(2.8), h = 100, center = true);
        }
	}
}

module bolex_pin_laser (x, y) {
	in = innerD;
    $fn = 120;
	translate ([x, y, 1]) {
		difference () {
			union () {
				translate([0, 0, (height / 2) - 3]) cylinder(r = R(outerD + 5), h = 2, center = true);
				translate([0, 0, 1.175/2]) cylinder(r = R(outerD), h = height + 1.175 , center = true);
			}
			cylinder(r = in / 2, h = height * 2, center = true);
			translate([0, 0, (height / 2) - 1.9]) cylinder(r1 = R(4.5), r2 = R(6.7), h = 2, center = true);
            translate([0, 0, (height / 2) + 1]) cylinder(r = R(6.7), h = 4, center = true);
		}
	}
}

module intval_laser_standoffs () {
    $fn = 40;
    for (i = [0 : len(xArray) - 1]) {
        bolex_pin_laser(xArray[i], yArray[i]);
	}
}

module intval_laser_standoffs_plate () {
    $fn = 40;
    rotate ([0, 180, 0]) {
        bolex_pin_laser(0, 0);
        bolex_pin_laser(15, 0);
        bolex_pin_laser(0, 15);
        bolex_pin_laser(15, 15);
    }
    //decoys
    //translate([7, 7, 0]) decoys(23, 5.5, 6);
}

module bolex_pin_inner_laser (x, y) {
    $fn = 40;
    //innerD = 6.75;
    innerD = 9;
	translate ([x, y, 1]) {
		cylinder(r = R(innerD), h = height * 2, center = true);
		//translate([0, 0, (height / 2) - 1]) cylinder(r1 = R(4.5), r2 = R(6.5), h = 2, center = true);
	}
}

module bearing_laser (x, y, z, width= 8, hole = true) {
	innerD = 8.05;
	outerD = 21.7;
	fuzz = 0.1;
	translate ([x, y, z]) {
		difference () {
			cylinder(r = R(outerD) + fuzz, h = width, center = true);
			if (hole) {
				cylinder(r = R(innerD) - fuzz, h = width, center = true);
			}
		}
	}
}

module intval_laser_panel_cover (LASER = false, DEBUG = false, ALL_RED = false, PCB = false, buttons = true, logo = false, DC_D = 10.9, PAD = 0, BOLTS = true, printed = false) {
    $fn = 60;
    cover_h = 38; //16 + 3 + 4 + 15;
    MATERIAL = IN / 8;
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

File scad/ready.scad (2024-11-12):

//!OpenSCAD
/* preprocessor */

IN = 25.4;
MM = 1;

function R (diameter) = diameter / 2.0;

function IN2MM(in) = in * IN;

function MM2IN(mm) = mm / IN;

module hex (diag = 10, h = 1) {
  cylinder(r = diag / 2, h = h, center = true, $fn = 6);
}

module tube(o = 1, i = 0, h = 1, center = false, $fn = 12) {
	$fn = $fn;
	union () {
		difference () {
			cylinder(r = o, h = h, center = center);
			cylinder(r = i,  h = h, center = center);
		}
	}
}

module rounded_cube (cube_arr = [1, 1, 1], d = 0, center = false) {
	off_x = 0;
	off_y = 0;
	r = d/2;
	union () {
		cube([cube_arr[0] - d, cube_arr[1], cube_arr[2]], center = center);
		cube([cube_arr[0], cube_arr[1] - d, cube_arr[2]], center = center);
		translate ([1 * (cube_arr[0] / 2) - r , 1 * (cube_arr[1] / 2)- r, 0]) cylinder(r = r, h = cube_arr[2], center = center);
		translate ([-1 * (cube_arr[0] / 2) + r, -1 * (cube_arr[1] / 2) + r, 0]) cylinder(r = r, h = cube_arr[2], center = center);
		translate ([1 * (cube_arr[0] / 2) - r, -1 * (cube_arr[1] / 2) + r, 0]) cylinder(r = r, h = cube_arr[2], center = center);
		translate ([-1 * (cube_arr[0] / 2) + r, 1 * (cube_arr[1] / 2)- r, 0]) cylinder(r = r, h = cube_arr[2], center = center);
	}
}

/*rounded_cube mikowski - avoid on web for triangulation errors\
NOT READY FOR PRIMETIME
module round_cube_minkowski (c = [1, 1, 1], diameter = 1) {
	minkowski() {
		cube([c[0] - diameter, c[1] - diameter, diameter(c[2])], center = true);
		cylinder(r = diameter(diameter), h = c[2] / 2, center = true);
	}
}
*/

module c_battery () {
	/* C Cell battery, 26.1 × 50 */
	x = 26.1;
	x_fuzz = .3;
	y = 50;
	y_fuzz = 2;
	cylinder(r = (x + x_fuzz) / 2, h = y + y_fuzz, center = true);
}

module sub_c_battery () {
	/* Sub C Cell battery, 22.2 × 42.9 */
	x = 22.2;
	x_fuzz = .3;
	y = 42.9;
	y_fuzz = 2;
	cylinder(r = (x + x_fuzz) / 2, h = y + y_fuzz, center = true);
}

module hex (r = 1, h = 1, center = false) {
	cylinder(r = r, h = h, center = center, $fn = 6);
}

module triangle (a = 1, b = 1, c = 1, h = 1, center = false) {
	
}

module cone_45 (d = 1, center = false) {
	cylinder(r1 = d/2, r2 = 0, h = d, center = center);
}

module decoys (d = 10, z = 0, number = 4, cube_size = 4, debug = false) {
        for (i = [0: number]) {
            rotate([0, 0, (360/number) * i]) translate([d, 0, z]) cube([cube_size, cube_size, cube_size], center = true);
            if (debug && i == 0) {
                rotate([0, 0, (360/number) * i]) translate([d, 0, z]) cube([cube_size * 5, cube_size* 5, cube_size], center = true);
            }
        }
}

//////////////////////////////////////////////////////////////////////////////////////////////
// Paraboloid module for OpenScad
//
// Copyright (C) 2013  Lochner, Juergen
// http://www.thingiverse.com/Ablapo/designs
//
// This program is free software. It is 
// licensed under the Attribution - Creative Commons license.
// http://creativecommons.org/licenses/by/3.0/
//////////////////////////////////////////////////////////////////////////////////////////////

module paraboloid (y=10, f=5, rfa=0, fc=1, detail=44){
	// y = height of paraboloid
	// f = focus distance 
	// fc : 1 = center paraboloid in focus point(x=0, y=f); 0 = center paraboloid on top (x=0, y=0)
	// rfa = radius of the focus area : 0 = point focus
	// detail = $fn of cone

	hi = (y+2*f)/sqrt(2); // height and radius of the cone -> alpha = 45° -> sin(45°)=1/sqrt(2)
	x =2*f*sqrt(y/f); // x  = half size of parabola
	
   translate([0,0,-f*fc]) // center on focus 
	rotate_extrude(convexity = 10,$fn=detail ) // extrude paraboild
	translate([rfa,0,0]) // translate for fokus area	 
	difference(){
		union(){ // adding square for focal area
			projection(cut = true) // reduce from 3D cone to 2D parabola
				translate([0,0,f*2]) rotate([45,0,0]) // rotate cone 45° and translate for cutting
				translate([0,0,-hi/2])cylinder(h= hi, r1=hi, r2=0, center=true, $fn=detail); // center cone on tip
			translate([-(rfa+x ),0]) square ([rfa+x , y ]); // focal area square
		}
		translate([-(2*rfa+x ), -1/2]) square ([rfa+x ,y +1] ); 					// cut of half at rotation center 
	}
}

//Spiral Notes
//-------------------------------------------------------------------
//Height = center to center height of the end spheres which form the spirals.  Ends will need to be flattened by the user as desired.  Actual height of the rendering is Height+2*baseRadius
//Radius = the maximum distance from the axis of the spiral (the z axis) to the center of the sphere(s) forming the spiral
//baseRadius = cross sectional radius of the spiral
//frequency = the number of complete revolutions about the axis made by the spiral, whole numbers will result in spirals whose tops end directly above their bases
//resolution = integer number of spheres, not to be confused with $fn.  The greater the number of spheres, the smoother the spiral will be (also longer render times!).  Recommended that this number be 8*frequency or greater.
//numSpirals = integer number of spirals used in the spiralMulti modules spaced evenly around the axis (3 spirals are spaced 120 degrees apart, 4 spirals: 90 degrees apart, etc.) 

//Instructions
//------------------------------------------------------------------
//1. Place spiral.scad in the "libraries" folder of your openscad installation.  Find the libraries folder by File -> Show Library Folder...
//2. Then create a new or open one of your existing scad files and include spiral.scad with the following code:  
//use<spiral.scad>;
//3. Then call the modules in your files with code similar to the following:
//spiral(20,20,3,1,25);
//spiralCone(20,20,3,1,25);
//spiralEllipse(20,20,3,1,25);
//spiralMulti(20,20,3,1,25,3);
//spiralMultiCone(20,20,3,1,25,3);
//spiralMultiEllipse(40,60,3,1,32,3);

//-------------------------------------------------------------
//simple spiral
module spiral (height = 20, Radius = 20, baseRadius = 3, frequency = 1, resolution = 25, $fn=50) {
	union(){
		translate ([0,0,-(height/2)]) {
				for(i=[0:resolution-2]){
					hull(){
						rotate ([0,0,frequency*360/(resolution-1)*i]) translate ([Radius,0,i*height/(resolution-1)]) sphere(r=baseRadius, center=true);
						rotate ([0,0,frequency*360/(resolution-1)*(i+1)]) translate ([Radius,0,(i+1)*height/(resolution-1)]) sphere(r=baseRadius,center=true);
					}
				}
		}
	}
}

//cone spiral
module spiralCone(height=20,Radius=20,baseRadius=3,frequency=1,resolution=25, $fn=50) {
	union(){
		translate ([0,0,-(height/2)]) {
				for(i=[0:resolution-2]){
					hull(){
						rotate ([0,0,frequency*360/(resolution-1)*i]) translate ([Radius-(i-1)*Radius/resolution,0,i*height/(resolution-1)]) sphere(r=baseRadius, center=true);
						rotate ([0,0,frequency*360/(resolution-1)*(i+1)]) translate ([Radius-i*Radius/resolution,0,(i+1)*height/(resolution-1)]) sphere(r=baseRadius,center=true);
					}
				}
		}
	}
}

//ellipse spiral
module spiralEllipse(height=20,Radius=20,baseRadius=3,frequency=1,resolution=25, $fn=50) {
	union(){
		translate ([0,0,-(height/2)]) {
				for(i=[0:resolution-2]){
					hull(){
						rotate ([0,0,frequency*360/(resolution-1)*i]) translate ([Radius*sqrt(1-(i/(resolution-1)*(i/(resolution-1)))),0,i*height/(resolution-1)]) sphere(r=baseRadius, center=true);
						rotate ([0,0,frequency*360/(resolution-1)*(i+1)]) translate ([Radius*sqrt(1-((i+1)/(resolution-1)*((i+1)/(resolution-1)))),0,(i+1)*height/(resolution-1)]) sphere(r=baseRadius,center=true);
					}
				}
		}
	}
}

// Multiple spirals arranged radially around the axis
module spiralMulti(height=20,Radius=20,baseRadius=3,frequency=1,resolution=25,numSpirals=3,$fn=50) {
	shiftAngle=360/numSpirals;
	for(total=[0:numSpirals-1]) {
		union(){
		translate ([0,0,-(height/2)]) {
					for(i=[0:resolution-2]){
						hull(){
							rotate ([0,0,frequency*360/(resolution-1)*i+shiftAngle*total]) translate ([Radius,0,i*height/(resolution-1)]) sphere(r=baseRadius, center=true);
							rotate ([0,0,frequency*360/(resolution-1)*(i+1)+shiftAngle*total]) translate ([Radius,0,(i+1)*height/(resolution-1)]) sphere(r=baseRadius,center=true);
						}
					}
			}
		}
	}
}

// Multiple spirals arranged radially around the axis tapering in towards the axis
module spiralMultiCone(height=20,Radius=20,baseRadius=3,frequency=1,resolution=25,numSpirals=3,$fn=50) {
	shiftAngle=360/numSpirals;
	for(total=[0:numSpirals-1]) {
		union(){
			translate ([0,0,-(height/2)]) {
					for(i=[0:resolution-2]){
						hull(){
							rotate ([0,0,frequency*360/(resolution-1)*i+shiftAngle*total]) translate ([Radius-(i-1)*Radius/resolution,0,i*height/(resolution-1)]) sphere(r=baseRadius, center=true);
							rotate ([0,0,frequency*360/(resolution-1)*(i+1)+shiftAngle*total]) translate ([Radius-i*Radius/resolution,0,(i+1)*height/(resolution-1)]) sphere(r=baseRadius,center=true);
						}
					}
			}
		}
	}
}
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

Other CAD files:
dxf/intval2_panel.dxf
dxf/intval2_panel_cover.dxf
dxf/intval2_laser_plate.dxf
stl/intval2_printed_panel_cover.stl
dist/intval2_electronics_mount.stl
dist/intval2_electronics_mount_metro.stl
dist/intval2_key_cap.stl
dist/intval2_motor_cap.stl
dist/intval2_motor_key.stl
dist/intval2_motor_key_120.stl
dist/intval2_motor_key_ALT1.stl
dist/intval2_motor_mount_bottom.stl
dist/intval2_motor_mount_top.stl
dist/intval2_motor_mount_top_120.stl
dist/intval2_panel_cover_laser.dxf
dist/intval2_plunger_plate.stl
dist/intval2_stl_plate.stl
stl/intval2_bearing_reinforcement.stl
stl/intval2_bolt_guide.stl
stl/intval2_button_nuts_plate.stl
stl/intval2_case_standoff.stl
stl/intval2_electronics_mount.stl
stl/intval2_key_cap.stl
stl/intval2_l298N_mount.stl
stl/intval2_motor_cap.stl
stl/intval2_motor_cap_120.stl
stl/intval2_motor_key.stl
stl/intval2_motor_key_120.stl
stl/intval2_motor_key_120_reinforced.stl
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

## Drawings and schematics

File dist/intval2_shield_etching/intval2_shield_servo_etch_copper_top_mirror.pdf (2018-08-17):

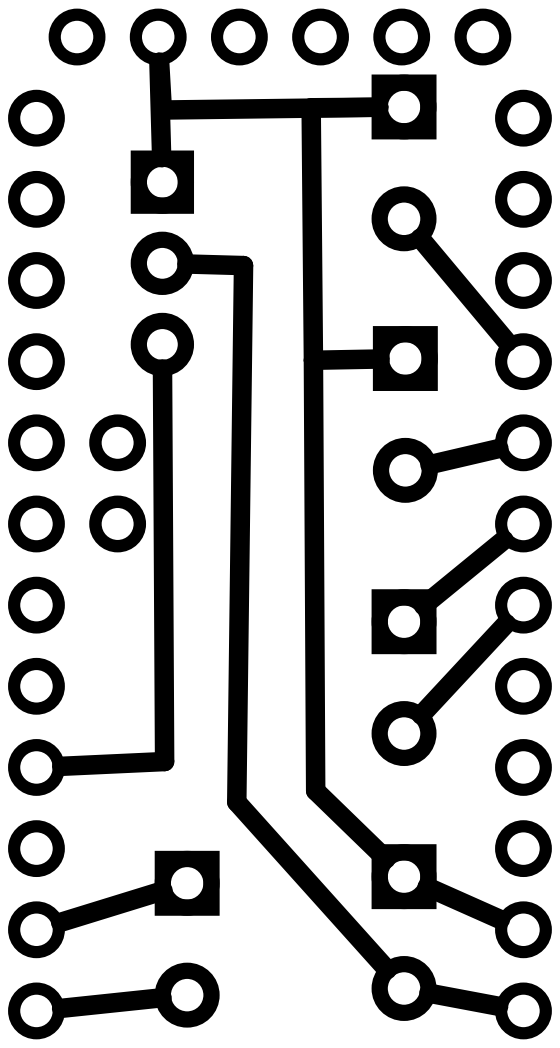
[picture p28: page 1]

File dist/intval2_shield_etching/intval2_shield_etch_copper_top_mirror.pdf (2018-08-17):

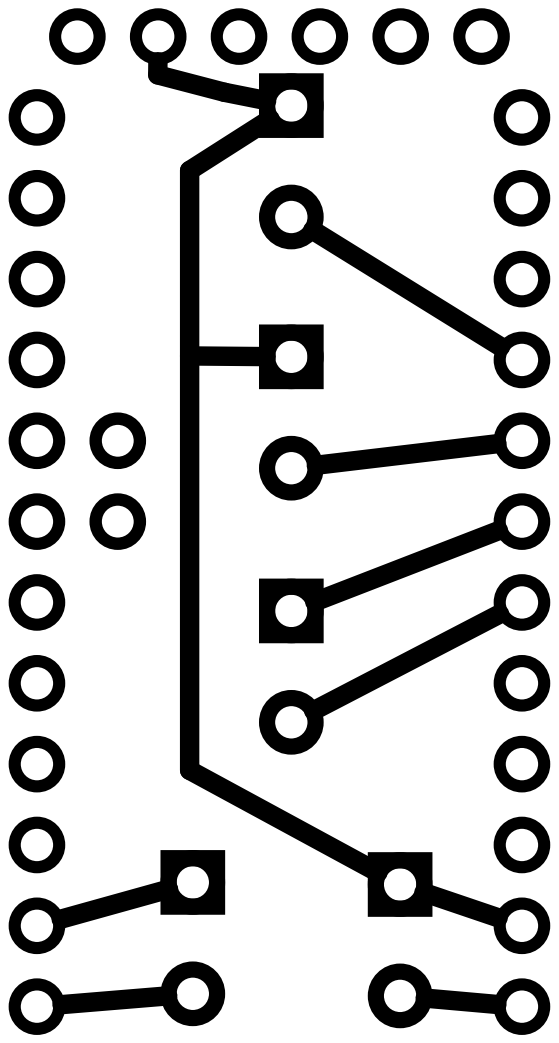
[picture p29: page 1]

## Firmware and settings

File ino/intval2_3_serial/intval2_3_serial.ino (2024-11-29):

#include "McopySerial.h"


//Can be controlled via serial, with mcopy and filmout_manager
//Buttons are optional
//Exposure controls assumes use  of a 120RPM motor
//Uses L298N H-bridge breakout board
//Target board is an Arduino Nano

/*
----------------------------------------------------
Microswitch (use INPUT_PULLUP!!)
GND-----\ | \-----PIN
----------------------------------------------------
*/

const int MOTOR_RPM = 120;
const int BOLEX_C = round((133 / (1.66 * 360)) * 1000); //bolex exposure constant
const int FAST_PWM = 255;

/* ------------------------------------------------
 *  pins
 * ------------------------------------------------*/
//Arduino Nano
const int PIN_INDICATOR = 13;
const int PIN_MOTOR_FORWARD = 9;
const int PIN_MOTOR_BACKWARD = 10;
const int PIN_MICRO = 19;
//6, 5, 4
//1, 2, 3
const int BUTTON[4] = {3, 4, 5, 6};  //trigger, delay, speed, direction

/* ------------------------------------------------
 *  loop
 * ------------------------------------------------*/
const int LOOP_DELAY = 10;

/* ------------------------------------------------
 *  state
 * ------------------------------------------------*/
volatile int button_state[4] = {1, 1, 1, 1};
volatile long button_time[4] = {0, 0, 0, 0};
volatile long buttontime = 0;

volatile boolean sequence = false;
volatile boolean running = false;
volatile boolean cam_dir = true;
volatile boolean delaying = false;
volatile boolean timed = false;

volatile int counter = 0;

volatile int micro_position = 0;
volatile boolean micro_primed = false;

unsigned long timer = 0;
unsigned long frame_start = 0;
unsigned long delay_start = 0;

String timed_str = "600";
unsigned long timed_val = 600;
unsigned long timed_open = 300; //ms after start_frame to pause
volatile boolean timed_paused = false;
unsigned long timed_delay = 0;
unsigned long timed_last = 0;
unsigned long timed_avg = 600;

volatile int fwd_speed = FAST_PWM;
volatile int bwd_speed = FAST_PWM;

volatile long seq_delay = 42;
volatile boolean is_open = false;

/* ------------------------------------------------
 *  serial
 * ------------------------------------------------*/
McopySerial mc;
volatile char cmd_char = 'z';

const int serialDelay = 5;

void setup() {
  mc.begin(mc.CAMERA_IDENTIFIER);
  PinsInit();
  ButtonsInit();
}

void loop() {
  cmd_char = mc.loop();
  cmd(cmd_char);

  timer = millis();
  
  Button(0);
  Button(1);
  Button(2);
  Button(3);
  
  if (sequence && delaying) {
    WatchDelay();
  }
  
  if (running) {
    if (timed) {
     ReadTimed();  
    } else {
     ReadMicro(); 
    }
  }
  if (!running && !sequence && !delaying){ 
    delay(LOOP_DELAY);
  }
}

void cmd (char val) {
  if (val == mc.CAMERA) {
    Camera();
  } else if (val == mc.CAMERA_FORWARD) {
    CameraDirection(true);
  } else if (val == mc.CAMERA_BACKWARD) {
    CameraDirection(false);
  } else if (val == mc.CAMERA_OPEN) {
    CameraOpen();
  } else if (val == mc.CAMERA_CLOSE) {
    CameraClose();
  } else if (val == mc.CAMERA_EXPOSURE) {
    CameraExposure();  
  } else if (val == mc.STATE) {
    State();
  }
}

//sending "0" will reset to default exposure time
void CameraExposure () {
  timed_str = mc.getString();
  timed_val = timed_str.toInt();
  if (timed_val < 600) {
    timed_val = 600;
    timed_str = "600";
    timed = false;
  } else {
    timed_delay = timed_val - BOLEX_C;
    timed = true;
  }
  mc.confirm(mc.CAMERA_EXPOSURE);
  mc.log("Set exposure time to: ");
  mc.log(timed_str);
}

void PinsInit () {
  pinMode(PIN_MOTOR_FORWARD, OUTPUT);
  pinMode(PIN_MOTOR_BACKWARD, OUTPUT);
  pinMode(PIN_MICRO, INPUT_PULLUP);
  pinMode(PIN_INDICATOR, OUTPUT);
}

void ButtonsInit () {
  for (int i = 0; i < 4; i++) {
    pinMode(BUTTON[i], INPUT_PULLUP);
  }
}

void Button (int index) {
  int val = digitalRead(BUTTON[index]);
  if (val != button_state[index]) {
    if (val == LOW) { // pressed
      button_time[index] = millis();
      //button_start(index);
    } else if (val == HIGH) { // not pressed
      buttontime = millis() - button_time[index];
      ButtonEnd(index, buttontime);
    }
  }
  button_state[index] = val;
}

/*
 * dormant for now
 * void button_start (int index) {
  if (index == 0) {
  }
}*/

void ButtonEnd (int index, long buttontime) {
  if (index == 0) {
    if (buttontime > 1000) {
      if (!sequence && !running) {
        sequence = true;
        Output(2, 75);
        Camera();
      }
    } else {
       if (sequence) {
        sequence = false;
        //Output(2, 75);
      } else {
         Camera();
      }
    }
  } else if (index == 1) { //set delay
    if (buttontime < 42) {
      seq_delay = 42;
      Output(1, 500);
    } else {
      seq_delay = buttontime;
      Output(2, 250);
    }
  }  else if (index == 2) { // set speed
    if (buttontime >= 1000) {
      timed_delay = buttontime - BOLEX_C;
      timed = true;
      Output(2, 250);
    } else if (buttontime < 1000) {
      timed_delay = 0;
      timed = false;
      Output(1, 500);    
    }
  } else if (index == 3) { //set direction
    if (buttontime < 1000) {
      cam_dir = true;
      Output(1, 500);
    } else if (buttontime > 1000) {
      cam_dir = false;
      Output(2, 250);
    }
  }
  buttontime = 0;
}

void Indicator (boolean state) {
  if (state) {
    digitalWrite(PIN_INDICATOR, HIGH);
  } else {
    digitalWrite(PIN_INDICATOR, LOW);
  }
}

void Output (int number, int len) {
  for (int i = 0; i < number; i++) {
    Indicator(true);
    delay(len);
    Indicator(false);
    delay(42);
  }
}

void Camera () {
  frame_start = millis();
  if (cam_dir) {
    analogWrite(PIN_MOTOR_FORWARD, fwd_speed);
    analogWrite(PIN_MOTOR_BACKWARD, 0);
  } else {
    analogWrite(PIN_MOTOR_BACKWARD, bwd_speed);
    analogWrite(PIN_MOTOR_FORWARD, 0);
  }
  running = true;
  micro_primed = false;
}

void CameraOpen () {
  if (cam_dir) {
    analogWrite(PIN_MOTOR_FORWARD, fwd_speed);
    analogWrite(PIN_MOTOR_BACKWARD, 0);
  } else {
    analogWrite(PIN_MOTOR_BACKWARD, bwd_speed);
    analogWrite(PIN_MOTOR_FORWARD, 0);
  }
  running = true;
  micro_primed = false;
  
  delay(timed_open);

  analogWrite(PIN_MOTOR_FORWARD, 0);
  analogWrite(PIN_MOTOR_BACKWARD, 0);

  micro_position = digitalRead(PIN_MICRO);
  if (micro_position == LOW) {
    micro_primed = true;
  }

  mc.confirm(mc.CAMERA_OPEN);
  mc.log("camera_open()");
  is_open = true;
  running = false;
}

void CameraClose () {
  bool microswitch_open = false;
  if (is_open) {
    if (cam_dir) {
      analogWrite(PIN_MOTOR_FORWARD, fwd_speed);
      analogWrite(PIN_MOTOR_BACKWARD, 0);
    } else {
      analogWrite(PIN_MOTOR_BACKWARD, bwd_speed);
      analogWrite(PIN_MOTOR_FORWARD, 0);
    }

    while (!microswitch_open) {
      micro_position = digitalRead(PIN_MICRO);
      if (micro_position == HIGH) {
        microswitch_open = true;
      }
      delay(2);
    }
    delay(10);

    analogWrite(PIN_MOTOR_FORWARD, 0);
    analogWrite(PIN_MOTOR_BACKWARD, 0);
  } else {
    micro_position = digitalRead(PIN_MICRO);
    if (micro_position == HIGH) {
      mc.log("WARNING: Camera already closed");
    }
  }
  mc.confirm(mc.CAMERA_CLOSE);
  mc.log("camera_close()");
  is_open = false;
}

boolean ReadDelay () {
  if (timer - frame_start >= timed_open) {
    return true;
  }
  return false;
}

void WatchDelay () {
  if (timer - delay_start >= seq_delay) {
    delaying = false;
    Camera();
  }
}

void ReadTimed () {
  if (!timed_paused) {
    if (timer - frame_start > timed_open 
      && timer - frame_start < timed_open + timed_delay) {
       PauseTimed();
    } else if (timer - frame_start > timed_open + timed_delay) {
      micro_position = digitalRead(PIN_MICRO);
      if (micro_position == HIGH) {
        Stop();
      }
      delay(2);//smooths out signal  
    }
  } 
  if (timed_paused && timer - frame_start > timed_open + timed_delay) {
    StartTimed();   
  }
}

void PauseTimed () {
  timed_paused = true;
  analogWrite(PIN_MOTOR_FORWARD, 0);
  analogWrite(PIN_MOTOR_BACKWARD, 0);
}

void StartTimed () {
  timed_paused = false;
   if (cam_dir) {
    analogWrite(PIN_MOTOR_FORWARD, fwd_speed);
    analogWrite(PIN_MOTOR_BACKWARD, 0);
  } else {
    analogWrite(PIN_MOTOR_BACKWARD, bwd_speed);
    analogWrite(PIN_MOTOR_FORWARD, 0);
  } 
}

void ReadMicro () {
  if (ReadDelay()) {
    micro_position = digitalRead(PIN_MICRO);
    if (micro_position == LOW 
        && micro_primed == false) {
      micro_primed = true;
    } else if (micro_position == HIGH 
              && micro_primed == true) {
      Stop();
    }
    delay(2);//smooths out signal
  }
}

void Stop () {
  delay(10);
  analogWrite(PIN_MOTOR_FORWARD, 0);
  analogWrite(PIN_MOTOR_BACKWARD, 0);
  
  running = false;
  micro_primed = false;

  if (cam_dir) {
    counter += 1;  
  } else {
    counter -= 1;
  }

  timed_last = timer - frame_start;
  timed_avg = (timed_avg + timed_last) / 2;

  mc.confirm(mc.CAMERA);
  mc.log("Camera completed");
  mc.log(String(timed_last));
  if (sequence) {
    delaying = true;
    delay_start = millis();
  }
}

void CameraDirection (boolean state) {
  cam_dir = state;
  if (state) {
    timed_open = 300;
    mc.confirm(mc.CAMERA_FORWARD);
    mc.log("camera_direction(true)");
  } else {
    timed_open = 400;
    mc.confirm(mc.CAMERA_FORWARD);
    mc.log("camera_direction(false)");
  }
}

void State () {
  String stateString = String(mc.STATE);
  stateString += String(mc.CAMERA_EXPOSURE);
  stateString += String(timed_avg);
  stateString += String(mc.STATE);
  mc.sendString(stateString);
}

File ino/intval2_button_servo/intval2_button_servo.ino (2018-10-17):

#include <Servo.h>



//Intval for pro trinket arduinos
//Using 12vdc motors in place of a stepper
//HBridge for motor control
//Microswitch for control

Servo blackout;

/*
----------------------------------------------------
Microswitch (use INPUT_PULLUP!!)
GND-----\ | \-----PIN
----------------------------------------------------
*/
const int MOTOR_RPM = 120;
const int BOLEX_C = round((133 / (1.66 * 360)) * 1000); //bolex exposure constant

const int FAST_PWM = 255;
const int SLOW_PWM = 127;

/* ------------------------------------------------
 *  pins
 * ------------------------------------------------*/
//Trinket Pro
const int PIN_INDICATOR = 13;
const int PIN_MOTOR_FORWARD = 9;
const int PIN_MOTOR_BACKWARD = 10;
//const int PIN_MICRO = 12;
const int PIN_MICRO = 19; //laser cut version
const int BUTTON[4] = {3, 6, 5, 4};  //trigger, direction, speed, delay


volatile int button_state[4] = {1, 1, 1, 1};
volatile long button_time[4] = {0, 0, 0, 0};
volatile long buttontime = 0;

/* ------------------------------------------------
 *  loop
 * ------------------------------------------------*/
const int LOOP_DELAY = 10;

/* ------------------------------------------------
 *  state
 * ------------------------------------------------*/
volatile int fwd_speed = FAST_PWM;
volatile int bwd_speed = FAST_PWM;

volatile boolean sequence = false;
volatile boolean running = false;
volatile boolean cam_dir = true;
volatile boolean delaying = false;
volatile boolean timed = false;

volatile int micro_position = 0;
volatile boolean micro_primed = false;

unsigned long timer = 0;
unsigned long frame_start = 0;
unsigned long delay_start = 0;

volatile int cam_count = 0;
volatile int cam_pos = 0;

unsigned long timed_open = 300; //ms after start_frame to pause
volatile boolean timed_paused = false;
unsigned long timed_delay = 0;
unsigned long timed_last = 0;
unsigned long timed_avg = 600;

volatile long seq_delay = 42;

volatile boolean black = true;
const int black_pin = 11;
const int black_pulse_width_min = 600; //TowerPro MG995
const int black_pulse_width_max = 2000; //TowerPro MG995
const int black_delay = 400;
const int black_start = 0;
const int black_end = 95;
const int black_timed = 1;
volatile boolean black_paused = false;


void setup () {
  blackout.attach(black_pin, black_pulse_width_min, black_pulse_width_max);
  Black_off();
  delay(1000);
  Black_on();
  
  Pins_init();
  Buttons_init();
}

void loop () {
  timer = millis();
  
  Btn(0);
  Btn(1);
  Btn(2);
  Btn(3);
  
  if (sequence && delaying) {
    Watch_delay();
  }
  
  if (running) {
    if (timed && !black) {
     Read_timed();  
    } else {
     Read_micro(); 
    }
  }
  if (!running && !sequence && !delaying){ 
    delay(LOOP_DELAY);
  }
}

void Pins_init () {
  pinMode(PIN_MOTOR_FORWARD, OUTPUT);
  pinMode(PIN_MOTOR_BACKWARD, OUTPUT);
  pinMode(PIN_MICRO, INPUT_PULLUP);
  pinMode(PIN_INDICATOR, OUTPUT);
}

void Frame () {
  frame_start = millis();
  if (cam_dir) {
    analogWrite(PIN_MOTOR_FORWARD, fwd_speed);
    analogWrite(PIN_MOTOR_BACKWARD, 0);
  } else {
    analogWrite(PIN_MOTOR_BACKWARD, bwd_speed);
    analogWrite(PIN_MOTOR_FORWARD, 0);
  }
  running = true;
  micro_primed = false;
}

void Pause_timed () {
  timed_paused = true;
  analogWrite(PIN_MOTOR_FORWARD, 0);
  analogWrite(PIN_MOTOR_BACKWARD, 0);
}

void Start_timed () {
  timed_paused = false;
   if (cam_dir) {
    analogWrite(PIN_MOTOR_FORWARD, fwd_speed);
    analogWrite(PIN_MOTOR_BACKWARD, 0);
  } else {
    analogWrite(PIN_MOTOR_BACKWARD, bwd_speed);
    analogWrite(PIN_MOTOR_FORWARD, 0);
  } 
}

boolean Read_delay () {
  if (fwd_speed == FAST_PWM) {
      if (timer - frame_start >= 300) {
        return true;
      }
  } else {
      if (timer - frame_start >= 600) {
        return true;
      }
  }
  return false;
}

void Watch_delay () {
  if (timer - delay_start >= seq_delay) {
    delaying = false;
    Frame();
  }
}

void Read_micro () {
  if (Read_delay()) {
    micro_position = digitalRead(PIN_MICRO);
    if (micro_position == LOW 
        && micro_primed == false) {
      micro_primed = true;
    } else if (micro_position == HIGH 
              && micro_primed == true) {
      Stop();
    }
    delay(2);//smooths out signal
  }
}

void Read_timed () {
  if (!timed_paused) {
    if (timer - frame_start > timed_open 
      && timer - frame_start < timed_open + timed_delay) { 
       Pause_timed();
       black_paused = true;
    } else if (timer - frame_start > timed_open + timed_delay) {
      micro_position = digitalRead(PIN_MICRO);
      if (micro_position == HIGH) {
        Stop();
      }
      delay(2);//smooths out signal  
    }
  }
  if (timed_paused && timer - frame_start > timed_open + timed_delay) {
    Start_timed();   
  }
}
void Stop () {
  delay(10);
  analogWrite(PIN_MOTOR_FORWARD, 0);
  analogWrite(PIN_MOTOR_BACKWARD, 0);
 
  cam_count++;
  if (cam_dir) {
    cam_pos++;
  } else {
    cam_pos--;
  }
  
  running = false;
  micro_primed = false;
  
  if (sequence) {
    if (black) {
      Black_on(); 
    } else {
      Black_off(); 
    }
    delaying = true;
    delay_start = millis();
  }
}

void Indicator (boolean state) {
  if (state) {
    digitalWrite(PIN_INDICATOR, HIGH);
  } else {
    digitalWrite(PIN_INDICATOR, LOW);
  }
}

void Buttons_init () {
  for (int i = 0; i < 4; i++) {
    pinMode(BUTTON[i], INPUT_PULLUP);
  }
}

void Btn (int index) {
  int val = digitalRead(BUTTON[index]);
  if (val != button_state[index]) {
    if (val == LOW) { // pressed
      button_time[index] = millis();
      //button_start(index);
    } else if (val == HIGH) { // not pressed
      buttontime = millis() - button_time[index];
      button_end(index, buttontime);
    }
  }
  button_state[index] = val;
}

/*
 * dormant for now
 * void button_start (int index) {
  if (index == 0) {
  }
}*/

void button_end (int index, long buttontime) {
  if (index == 0) {
    if (buttontime > 1000) {
      if (!sequence) {
        sequence = true;
        Output(2, 75);
        Frame();
      }
    } else {
      if (sequence) {
        sequence = false;
        //Output(2, 75);
      } else {
        //Output(2, 75);
        Frame();
      }
    }
  } else if (index == 1) { //set direction
    if (buttontime < 1000) {
      cam_dir = true;
      Output(1, 500);
    } else if (buttontime > 1000) {
      cam_dir = false;
      Output(2, 250);
    }
  } else if (index == 2) { // set speed
    if (buttontime >= 1000) {
      timed_delay = buttontime - BOLEX_C;
      timed = true;
      Output(2, 250);
    } else if (buttontime < 1000) {
      timed_delay = 0;
      timed = false;
      Output(1, 500);    
    }
  } else if (index == 3) { //set delay
    if (buttontime < 42) {
      seq_delay = 42;
      Output(1, 500);
    } else {
      seq_delay = buttontime;
      Output(2, 250);
    }
  }
  buttontime = 0;
}
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

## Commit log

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2015-04-28 Add hardware design
    Adds inval2.scad which can generate the hardware for 3d printing or
    other manufacturing.
    Very much in flux as electronics are being decided on.
    [intval2.scad]
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2016-01-11 Add readme.md
    [intval2.scad, ready.scad]
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2016-02-29 Clean up scad file for /dist
    [intval2.scad]
2016-02-29 Add all /dist files
    Includes dxf and stl files needed to build the INTVAL 2.0
    [intval2_electronics_mount.stl, intval2_key_cap.stl, intval2_motor_cap.stl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]
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2016-03-18 Intval2 fritzing file, initial commit
    [intval2.fzz]
2016-03-18 Import L298N model
    [intval2.fzz]
2016-03-19 Frizzing diagram completed
    [intval2.fzz]
2016-03-21 Improve schematics layout
    Still ugly as sin
    [intval2.fzz]
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2016-03-21 Added plate of all printable models
    [intval2.scad, intval2_stl_plate.stl]
2016-03-22 optimized plate layout for 150x150mm printer
    [intval2.scad, intval2_stl_plate.stl]
2016-03-22 Add dxf plate
    [intval2.scad, intval2_dxf_plate.dxf]
2016-03-22 Add exploded view for construction
    [intval2.scad]
2016-03-25 Improved motor key to allow hobbled shaft insertion
    [intval2.scad, intval2_motor_key.stl]
2016-03-29 Added alt motor_keys for different 1:1 shaft sizes
    [intval2.scad, intval2_motor_key_ALT1.stl]
2016-04-03 Made changes for 120RPM motors
    [intval2.scad]
2016-04-03 Increase resolution
    [intval2.scad]
2016-04-04 wider opening for motor mount
    [intval2.scad]
2016-04-04 Primary work on 120RPM motor mount
    [intval2.scad, intval2_motor_key_120.stl, intval2_motor_mount_top_120.stl]
2016-04-09 Move set screw to internal position in 120 key
    [intval2.scad, intval2_motor_key_120.stl]
2016-04-15 Add an altered version of the electronics mount for Arduino Metro Minis
    [intval2.scad]
2016-04-21 Add electronics mount for Adafruit Metro Mini
    Printed it, it works.
    [intval2_electronics_mount_metro.stl]
2016-04-21 Move stl into dist folder
    [intval2_electronics_mount_metro.stl]
2016-05-09 Make standoffs insert into laser cut panel
    This change will improve the physical structure of the panel. The
    standoffs will fit into enlarged holes in the panel so they can be
    glued to it.
    [intval2.scad]
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2016-05-12 Remove timer code, was doing nothing
    Will restore timer for Metro version of the firmware for profiling
    different motors. Doesn’t make sense here where the Trinket Pro can’t
    serial out.
    [intval2_buttons.ino]
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2016-05-13 Sequence no longer ends with an erroneous frame
    Moved the sequence start and stop logic into the button_end function.
    This will allow the sequence to stop without firing a final frame after
    the sequence is done. Also added variables to define the speed of the
    motors a little more easily.
    [intval2_buttons.ino]
2016-05-13 Redesigned 120RPM motor_key
    Needed to make it taller to have a better grip on the hobbled shaft.
    This change shifts the bolt that rests against the flat end of the
    shaft upwards, as well. May need to lift the bottom of the shaft
    negative space for more pressure against the key.
    [intval2.scad, intval2_motor_key_120.stl]
2016-05-13 Place motor key 120 in correct /dist folder
    [intval2_motor_key_120.stl]
2016-05-13 Add height to motor_key_120
    Also adjust the bottom of the hobbled shaft negative space so that the
    motor is required to put some force against the camera body.
    [intval2.scad, intval2_motor_key_120.stl]
2016-05-17 Update standoffs to better attach to panel
    Having built a number of these, attaching the standoffs is a problem.
    This is an attempt to better attach them to the panel.
    [intval2.scad, intval2_dxf_plate.dxf, intval2_panel_laser.dxf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]
2016-05-23 Create a motor cap for the 120RPM motor
    [intval2.scad, intval2_motor_cap_120.stl]
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2018-08-17 Shield work
    [intval2_shield.fzz]
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2018-08-21 Updated fritzing file
    [intval2.fzz]
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2018-09-24 Fix intval2_button_servo for new servo, add parameters which can change the pulse width for different models
    [intval2_button_servo.ino]
2018-10-09 Increase case height for a less crowded working area
    [intval2.scad]
2018-10-10 Fix case
    [intval2.scad]
2018-10-13 space out electronics for intval2
    [intval2.scad]
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2018-11-10 Add a bolt guide
    [intval2.scad]
2019-06-07 Made a board for oshpark
    [intval2_oshpark.fzz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]
2019-06-07 Removed board screenprinting.
    [intval2_oshpark.fzz]
2020-05-07 Add the 2.1 board design
    [intval2_1_oshpark.fzz]
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2021-05-02 Add reinforced key designs for default key and 120RPM variant.
    [intval2.scad, intval2_motor_key_120_reinforced.stl, intval2_motor_key_120_reinforced_roller.stl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]
2022-09-16 Add a bearing reinforcement piece
    [intval2.scad]
2022-09-16 Flatten side of bearing reinforcement to prevent obstructing the bolex variable shutter
    [intval2.scad]
2022-09-17 Slight adjustmetn forPrusa
    [intval2.scad]
2022-09-21 Add void for standoff on bearing reinforcement part
    [intval2.scad]
2022-09-24 Save standoff washer design for repairs
    [intval2.scad]
2022-10-07 Create Makefile and compile individual STL and DXF files for printing and laser cutting
    [intval2.scad, intval2_bolt_guide.stl, intval2_electronics_mount.stl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]
2022-10-08 Add remaining parts to Makefile
    [intval2.scad]
2022-10-08 Built all models
    [intval2_bearing_reinforcement.stl, intval2_bolt_guide.stl, intval2_case_standoff.stl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]
2022-10-08 Updated washer standoff
    [intval2.scad, intval2_case_standoff.stl]
2022-12-20 Add a reinforced motor mount top for alternate design
    [intval2.scad]
2022-12-20 Render missing stls
    [intval2.scad, intval2_button_nuts_plate.stl, intval2_l298N_mount.stl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]
2022-12-21 Re-render everying after error
    [intval2_bearing_reinforcement.stl, intval2_bolt_guide.stl, intval2_case_standoff.stl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]
2022-12-28 Fix the 120 roller
    [intval2.scad]
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2023-04-17 Make a printable version of the intval2 laser cut panel.
    [intval2.scad]
2023-04-17 Render the printed panel.
    [intval2_panel_printed.stl]
2023-04-28 Printable panel cover. Delete original intval1 design.
    [intval2.scad]
2023-05-03 Create an arduino_nano electronics mount
    [intval2.scad]
2023-06-29 Create an alternate motor cap for bigger motors
    [intval2.scad]
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2023-12-23 Tweaks needed for printing design
    [intval2.scad]
2024-05-29 Render all previously un-rendered STLs
    [intval2_arduino_nano_electronics_mount.stl, intval2_l289N_mount.stl, intval2_laser_plate.stl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]
2024-05-29 Correct wrongly-named l298N throughout SCAD file
    [intval2.scad]
2024-05-29 Accidentally rendered all files wrong. This corrects that. Add laser rendering of DXF files.
    [intval2.scad, intval2_arduino_nano_electronics_mount.stl, intval2_laser_plate.stl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]
2024-05-29 Fix laser render. Re-render all DXF files
    [intval2.scad, intval2_laser_plate.dxf, intval2_panel.dxf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]
2024-10-08 Add a set screw. Create a quickstart guide.
    [intval2.scad]
2024-11-12 Cleanup to OpenSCAD code. Add sorting to makefile. Use new linter for Openscad to clean up a lot of magic numbers.
    [intval2.scad, intval2_bearing_reinforcement.stl, intval2_bolt_guide.stl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]
2024-11-12 Add printed covers and update panel_printed with new bolts added
    [intval2.scad, intval2_printed_panel_cover.stl, intval2_printed_panel_cover_buttons.stl]
2024-11-12 Fixed rendering of printed panel. Removed panel_printed.stl (dumb).
    [intval2.scad, intval2_printed_panel.stl]
2024-11-14 Update the printed panel and the printed panel cover. Started building a BOM.
    [intval2.scad, intval2_printed_panel.stl, intval2_printed_panel_cover.stl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]
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2024-11-29 Render and normalize all parts. Use manifold option.
    [intval2.scad, intval2_arduino_nano_electronics_mount.stl, intval2_logo.stl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]
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2025-11-30 Fix bug with reporting set camera direction backwards as set camera forwards
    [Intval2.cpp, intval2_4_serial.ino]
2025-11-30 Through testing, found the ideal open_stop values for both thte forward and reverse position of the camera
    [Intval2.h]
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2025-12-12 Improve bulb logic. Also fixes issue with multiple frames running concurrently.
    [Intval2.cpp, Intval2.h]
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2025-12-14 Remove output vars for now, unneeded. Idea is to implement Output() to not use delays but there could be some problems especially if there are overlapping outputs. Not going to cross that bridge at t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
    [Intval2.h]
